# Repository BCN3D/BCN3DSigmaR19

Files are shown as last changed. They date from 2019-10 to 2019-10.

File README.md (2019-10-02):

## What’s hold in this repository?
This repository will hold all the information about the Mechanics of the BCN3D Sigma R19.
As a declared Open Source organization, it's in our mission to release all the original design files to you to be able to learn, reuse and improve. Open Source not only means code, it also concerns hardware.

We’ve managed to design and manufacture the BCN3D Sigma R19 thanks to our previous experience in the 3D printing industry, the ideas coming from the community, our engineering background and a narrow collaboration with our suppliers. Our goal is justify the decisions we took and share the know-how we acquired so far.

We also provide the source files for those who want to check the core of the BCN3D Sigma R19. You can consult both the CAD files and the technical drawings.

## CONCEPT DESIGN
During the concept design stage we set a clear target which determined the whole design and decisions: The BCN3D Sigma R19 is a professional printer.

### Aesthetics
It has to look  like a professional equipment. Our previous printers were made with aluminium extruded profiles and plastic printed parts. That made sense for printers oriented to makers or schools, sold as a kit. But, in this case, aesthetic was a major player. For this reason, we adopted a welded aluminium frame, which allows the Sigma to be a unique and attractive 3D printer

### Multimaterial
As a professional printer, it has to print as many materials as possible. Not only for engineers, who require tough -or flexible-, functional polymers, but also for designers who need the aesthetic component. However, material is not the only limitation. Complex geometries, overhangs and 3D printing doesn’t get along. So we wanted the Sigma to be a real solution for those users who need to print with supports as a must. In conclusion, the Sigma is the first and only commercial 3D printer with an Independent Dual Extuder (IDEX) system, which avoid all the side problems dual extrusion may cause.

### High Quality
The 3D Printing industry is maturing. Users are more and more demanding and 3D printing must be a solution, not a headache. For this reason, the Sigma has to be a reliable piece of engineering, easy to assemble, maintain and capable to print seamlessly high quality objects, no matter how complex they are.

### High Capacity
Real-life and functional parts are not always small. A big printing volume is a great advantage for a professional 3D Printer although the Sigma intends to be a desktop-sized printer. Allocating all the items and devices inside the frame, while granting ease-to-use and optimizing the axes structure were a key goal.

## DETAIL DESIGN INSIGHTS

We faced dozens of challenges during the design process. Below we describe some of them:

### Frame
Probably the biggest challenge. First we thought in a chassis made of profiles and then cover it. But then realized the cost in materials for that solution would be high enough to look for alternatives that could contribute more in the aesthetic field, even that could be a bit more expensive. On the other side, we wanted the Sigma to be an accessible printer, wide and open in order to ease the handling and operation. So we decided to explore the option of designing a unibody frame where all the mechanical components were mounted on and with a wide frontal oberture.

First we had to decide between using aluminium or steel. Steel offers many advantages: It’s a very stiff metal, great to build structures and precise mechanical systems. In addition, it’s easy to work with and cheap. But it’s -really- heavy. We contemplated the option of using a thinner metal sheet of steel for the frame. After ordering a prototype, we dismissed the idea, though. Still it had a great mechanical behaviour and a relative low weight, the feeling of touching a thin metal sheet (1.5mm) was unpleasant because it felt like a cutting edge. And it didn’t look sturdy. So to achieve both a reliable look and a pleasant contact, we needed to go up to 3mm thickness. But then the shipping costs would be absurdly high and the handling, a constant hassle -both during the assembly process and for the final user.

Aluminium, on the other hand, provides lightness and a smooth and sturdy look. But it’s more expensive as a material and it’s harder to laser cut and weld. After balancing pros and cons, we bet on aluminium option -although we had a plan B.

The second big issue to manage was the manufacturing process. We contemplated two different ways to do it: either manufacture the frame by parts and screw them all together in the assembly line or weld the frame. Welding aluminium is hard and the welding process itself has some thermal and geometric implications that have to be considered. But it allows to reduce the assembling time dramatically while it outsources a key process.

As alternative, designing the frame as separate parts to screw together was considerably cheaper - as you save a handmade process such as welding and polishing. But the assembling of the frame and adjustment could be very delicate and incompatible with our production tag time. So the overall cost wouldn’t be that different in both options. The aesthetic component, though, would be very penalized with this alternative, because we would need to add dozens of screws on the frame.

For these reasons, we finally opted for a welded structure. We sat hours with our supplier discussing the best way to design every single part in order to grant a proper alignment between the faces that would hold the axes. Furthermore, we also studied the mechanical behaviour of the frame with some CAE studies, simulating stress and deformations during a standard usage.

### High quality components
A good frame is not enough to achieve amazing results. In such a precision equipment as the Sigma, all the mechanical components play a key role. Due to the product requirements in terms of size and use of the internal space of the printer we had, we opted for a axes structure with the toolheads moving in the XY plane and an up and down moving Z axis.

With the XY plane decided to mount high precision linear guides. Despite its cost slightly higher than a system based on rods and bearings, the linear rails offer a professional look, an easy assembling and a compact package.

Regarding the Z axis, we were aware of the importance to have a robust guide system in order to avoid classic artifacts in printed parts related with a bad Z performance, such as Z wobbling. We also had experience using couplings and to connect the actuator with the leadscrew and we knew that a bad assembling could cause poor quality results. With this background, we chose using Ø12mm guide rods and a stepper motor with an inserted leadscrew. The whole system provides a high repeatability and accuracy.

### Independent Dual Extrusion
A 3D printer with such an specific feature increases the design unknowns and multiplies the components. Not only the firmware and the electronics need to be highly customized, but also mechanically there are some decisions to take.

First of all, because of the multiple components to hold, the internal parts tend to be more complex than other printers. So we decided to use aluminium sheet bending technology to manufacture the inner parts. As the manufacturing tolerances are acceptable for the purposes we intend and the technology is cheap and easily scalable, we considered the technology optimum.  

Two independent Extruders means have an extra moving stepper for the second toolhead, and the extra toolhead itself. On the other hand, when printing with both extruders it’s important to have a bucket to purge the idle hotends before start printing the model again. All this parts add weight to a moving element, which is a problem to print fast because the high inertias may worsen the print quality. So we designed the X and Y Axis as light as possible, saving as many grams as possible with every single component. Not only weight is important when doubling the toolheads, but also space. So we decided to adopt a bowden-based feeding system and miniaturize all the items as much as possible.

### Big Printing Volume
The BCN3D Sigma R19 features 210x297x210mm printing volume. In order to provide such a big volume and a free space on both sides to park the idle toolhead, but still having a desktop-sized printer, we had to reorient the Z platform. The main issue to solve, though, was granting the stiffness of the structure with a big overhang of more than 300mm.

To prevent vibrations, we adopted high quality bearings with low clearance and we designed and  simulated a custom metal sheet structure, which allows to get a great quality prints with a smooth surface despite the big overhang.

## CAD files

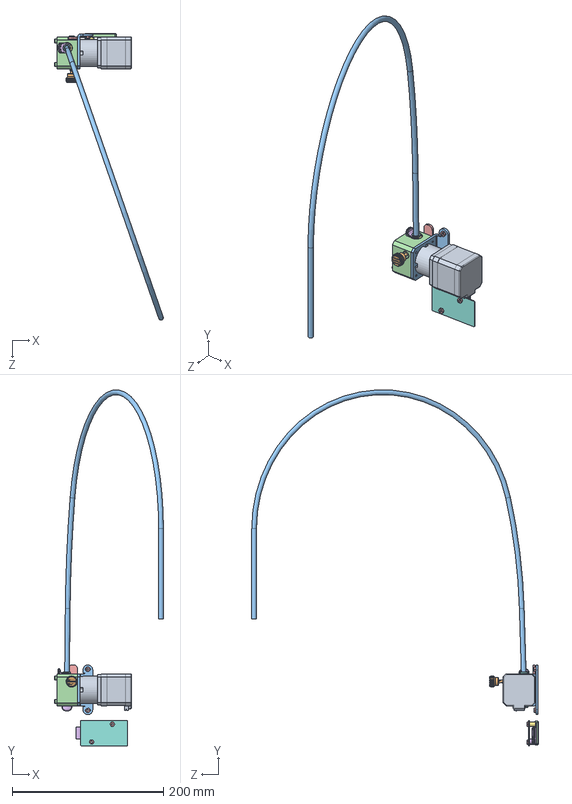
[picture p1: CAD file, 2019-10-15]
CAD/SW/040M07C01.0P000C Left extruder.SLDASM
143.8 x 470.4 x 378.6 mm
040M07C01.0P10A Nema 17 40mm
040M07C01.0P25Z Driving Gear
14080-a00_040M07C01.0P05E Extruder Stepper Holder
040M07C01.0P026E Extruder Body Left
040M07C01.0P027B Extruder Tensor Left
filament
10922-A00_Pneufit coupling x 2
10924-A00_Coupling collet x 2
Passador 4x24
BCN3DSigma-M05C01.0P08Z Purger Button
10982-A00_Bowden tube
A3DIN912 M3x30 x 3
A3DIN934 M3 x 4
040M04C00.0P03F Stepper Driver Board
Separador nylon negre 3.2x6x8 x 2
10918-A01_Extruder driver cover
A3DIN913 M3x3
DIN931 M4x50 (91280A154)
A3DIN912 M3x8 x 3
BCN3DSigma-M05C01.0P11F Driver spacer
BCN3DSigma-M04C00.0P09A Drivers Heatsink
BCN3DSigma-M07C01.0P14D Coupling Clip x 2

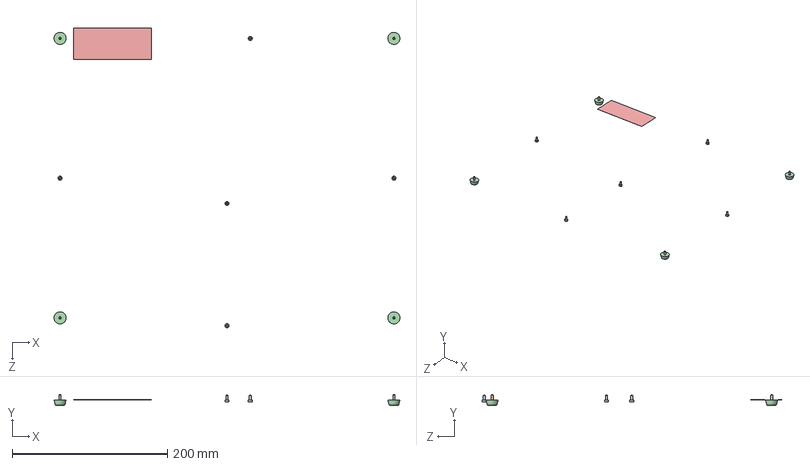
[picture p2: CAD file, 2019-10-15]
CAD/SW/BCN3DSigma-M01C03.0P000 Bottom cover.SLDASM
445.7 x 13.7 x 385.8 mm
DIN912 M3x6 x 5
DIN912 M3x10 x 4
DIN125 M3 x 4
BCN3DSigma-M01C03.0P02Z Leg x 4
BCN3DSigma-M01C01.0P25A Sigma CE Label

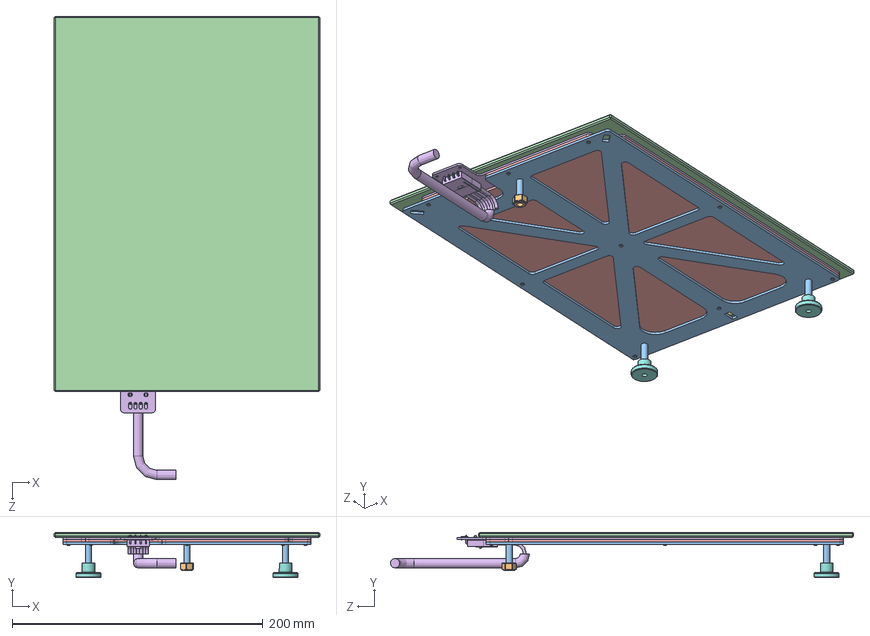
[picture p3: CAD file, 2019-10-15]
CAD/SW/BCN3DSigma-M03C02.0P000 Printing surface.SLDASM
212.0 x 36.1 x 369.2 mm
DIN7991 M3x6 x 9
DIN985 M5
10832-A00_Upper Platform
10906-A00_Cork
10908-A00_Heated bed
10888-A00 Bed Thumbscrew x 2
BCN3DSigma-M03C02.0P09A Thumbscrew Label x 2

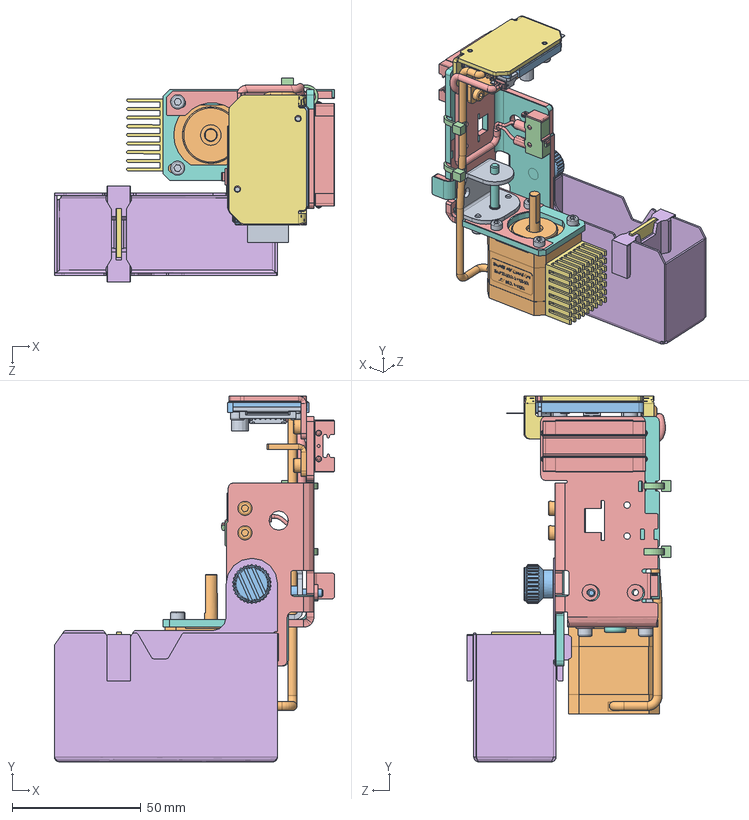
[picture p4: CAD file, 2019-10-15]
CAD/SW/BCN3DSigma-M05C02.0P000 X Axis Right.SLDASM
108.7 x 141.9 x 79.2 mm
DIN912 M3x6 x 8
DIN912 M3x8 x 6
DIN125 M3 poliamida x 2
DIN125 M3 x 2
10850-B00_Purger base right
040M05C02.0P04B X Stepper Driver Holder Right
BCN3DSigma-M02C01.0P10A Idler pulley shaft
BCN3DSigma-M04C00.0P03F Stepper Driver Board
10901-A00_Nema 14
BCN3DSigma-M05C01.0P08Z Purger Button
BCN3DSigma-M09C00.0P20A Zip tie x 2
Linear guide slide
Sigma_R17-M05C01.0P14D Cloth Support
BCN3DSigma-M05C01.0P07C Silicone Cloth
10828-A00_Stepper Holder Right
10830-B01_X Axis Idler
BCN3DSigma-M05C01.0P01D Belt Clamp
BCN3DSigma-M05C01.0P11F Driver spacer
BCN3DSigma-M02C01.0P08Z Endstop
BCN3DSigma-M09C00.0P15A Endstop X Right
BCN3DSigma-M04C00.0P09A Drivers Heatsink
040M05C01.0P017Z Heatsink 28x28x15

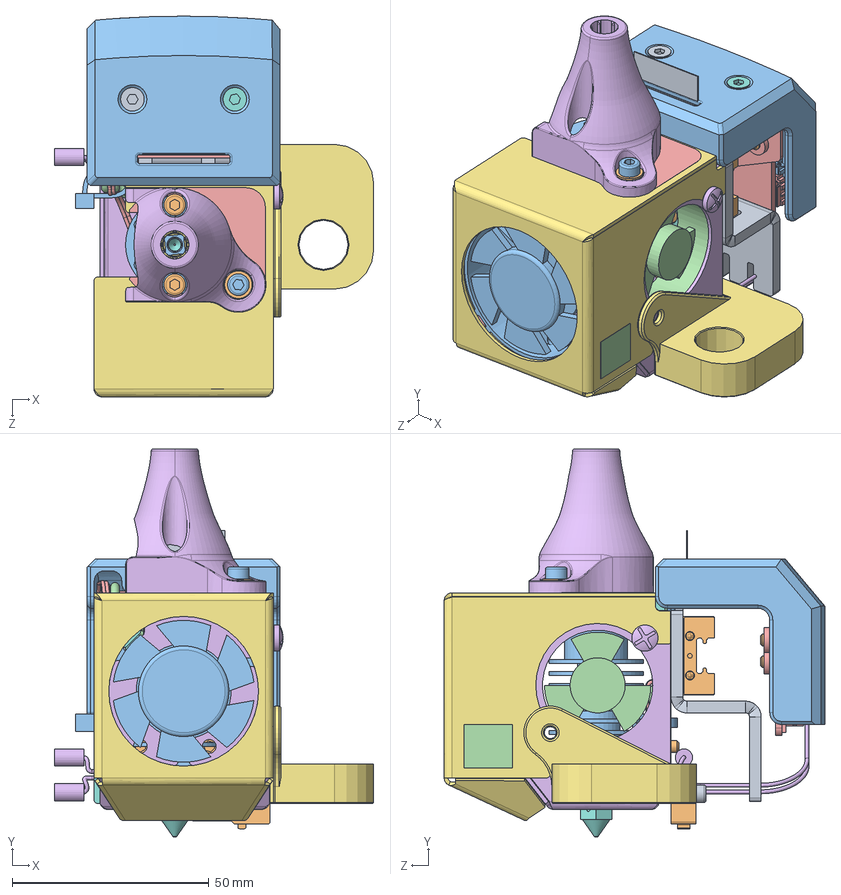
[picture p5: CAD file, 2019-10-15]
CAD/SW/040M06C01.0P000 Left Hotend.SLDASM
81.1 x 98.5 x 96.7 mm
A3DIN912 M2,5x10 x 2
A3DIN912 M3x6 x 8
A3DIN912 M3x10
A3DIN912 M3x8 x 2
A3DIN912 M3x18 x 3
A3DIN7981 9.5x3.2_RationalStock
A3DIN125 M3 poliamida x 4
A3DIN7991 M3x12
DIN7991 M3x12
A3DIN125 M3
BCN3DSigma-M06C01.0P01I Conexion Cover
040M06C01.0P03Z Heat sink fan
040M06C01.0P04C Connection board support
040M06C01.0P05E Lower cover
040M06C01.0P06D Upper cover
040M06C01.0P07D Hotend Plate
BCN3DSigma-M06C01.0P08F X Plate Left
040M06C01.0P09Z Layer fan
BCN3DSigma-M06C01.0P12B Layer fan spacer
040M04C00.0P04B Hotend Board
040M09C00.0P16B Endstop Z Left
A3DIN913 M3x3 x 2
040M06C03.0P01C Nozzle 0.4
040M06C03.0P02C Heatbreak
040M06C03.0P03A Hot block
040M06C03.0P04G Heatsink bowden
040M06C03.1P01B Resistance 24V
040M06C03.1P02B Thermistor
040M07C01.0P19Z Coupling collet
BCN3DSigma-M07C01.0P14D Coupling Clip
A3Connexio cable pla hotend
040M05C00.0P02ALinear guide slide
040M09C00.0P20A Zip tie
040M06C01.0P14A Hot surface Label
Nozzel Offset Shim 0.05mm A.5
040M06C01.0P15C Vertical bowden
Inductive Sensor Mount A1

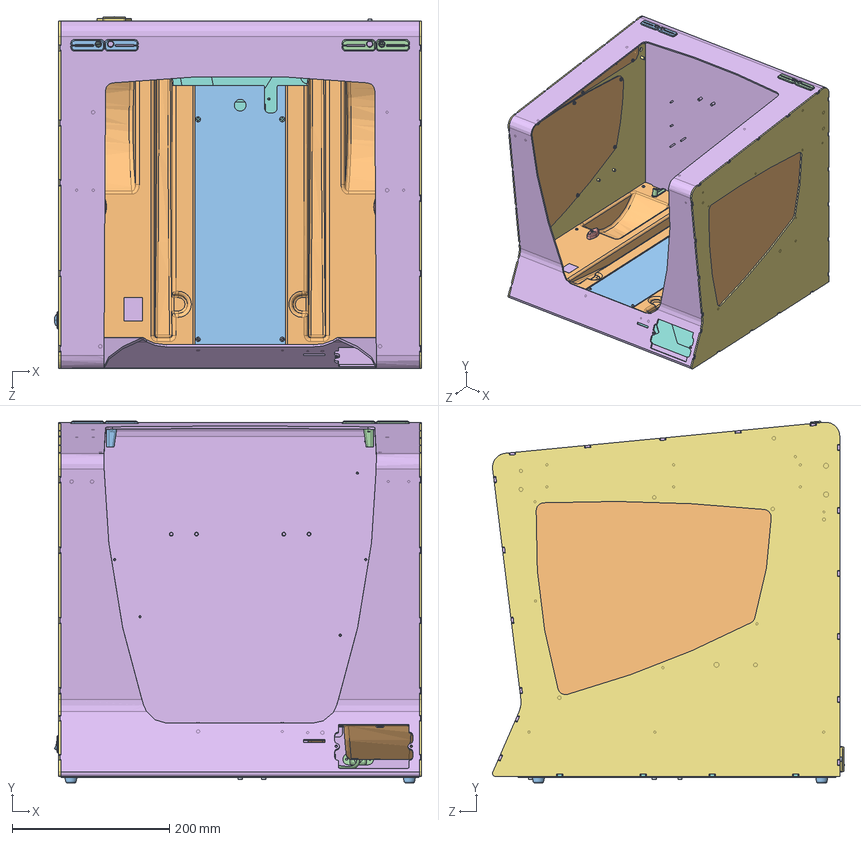
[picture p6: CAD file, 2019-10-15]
CAD/SW/BCN3DSigma-M01C00.0P000 Structure.SLDASM
466.9 x 459.6 x 447.2 mm
DIN125 M3 poliamida x 14
DIN934 M3 x 44
BCN3DSigma-M01C01.0P01J (RiT - Reverse Engineered) Top frame
BCN3DSigma-M01C01.0P03D (Test) Left_Right side x 2
BCN3DSigma-M01C01.0P02D (Test) Bottom frame
BCN3DSigma-M01C01.0P05D Y Idler Tensioner x 2
10894-A00_Window x 2
BCN3DSigma-M01C01.0P11Z Power button
BCN3DSigma-M01C01.0P12Z USB Extension Cable
BCN3DSigma-M01C01.0P20C Front LED connector clamp x 2
BCN3DSigma-M01C01.0P26C Hot bed cable double clip
BCN3DSigma-M04C00.0P07Z Power Entry Filter
BCN3DSigma-M01C01.0P17Z Fusible
BCN3DSigma-M01C01.0P30C Curve flat cable holder x 2
BCN3DSigma-M01C01.0P07G (Test) Guide spacer x 2
BCN3DSigma-M01C01.0P29H Bowden exit Left
BCN3DSigma-M01C01.0P29H Bowden exit Right
BCN3DSigma-M01C01.0P22D Plain flat cable holder x 4
BCN3DSigma-M01C01.0P15A Square 90 x 8
BCN3DSigma-M01C01.0P16A Square 60 x 2
DIN7981 3.2x9.5 x 6
ISO7380 M3x10 x 10
10890-A00_Inner cover 1.5mm
10891-A00_Electronics cover
BCN3DSigma-M01C02.0P06D Bowden entry guide x 2
BCN3DSigma-M01C02.P07F Bowden entry x 2
BCN3DSigma-M01C02.0P09A Crush Label
040M07C01.0P19Z Coupling collet x 2
10893-A00_Bottom cover
DIN912 M3x6 x 5
DIN912 M3x10 x 4
DIN125 M3 x 4
BCN3DSigma-M01C03.0P02Z Leg x 4
BCN3DSigma-M01C01.0P25A Sigma CE Label

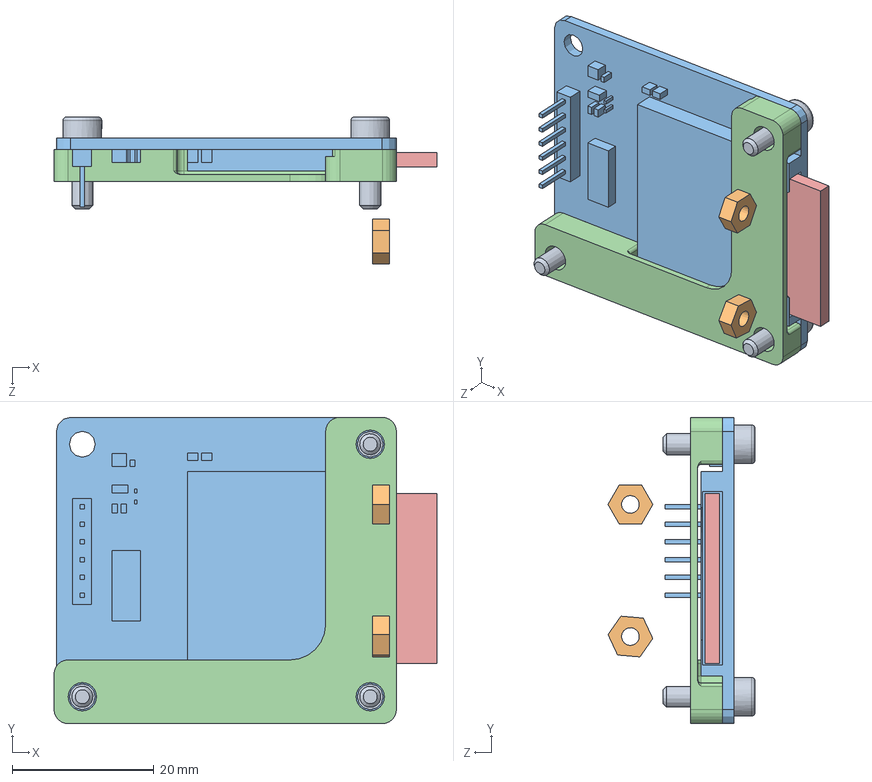
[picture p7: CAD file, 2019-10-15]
CAD/SW/BCN3DSigma-M04C02.0P000 SD Unit.SLDASM
54.1 x 43.2 x 20.8 mm
DIN912 M3x10 x 3
DIN934 M3 x 2
BCN3DSigma-M04C02.0P02AA SD module
BCN3DSigma-M04C02.0P03A SD spacer
BCN3DSigma-M04C02.0P04Z SD Card 8GB

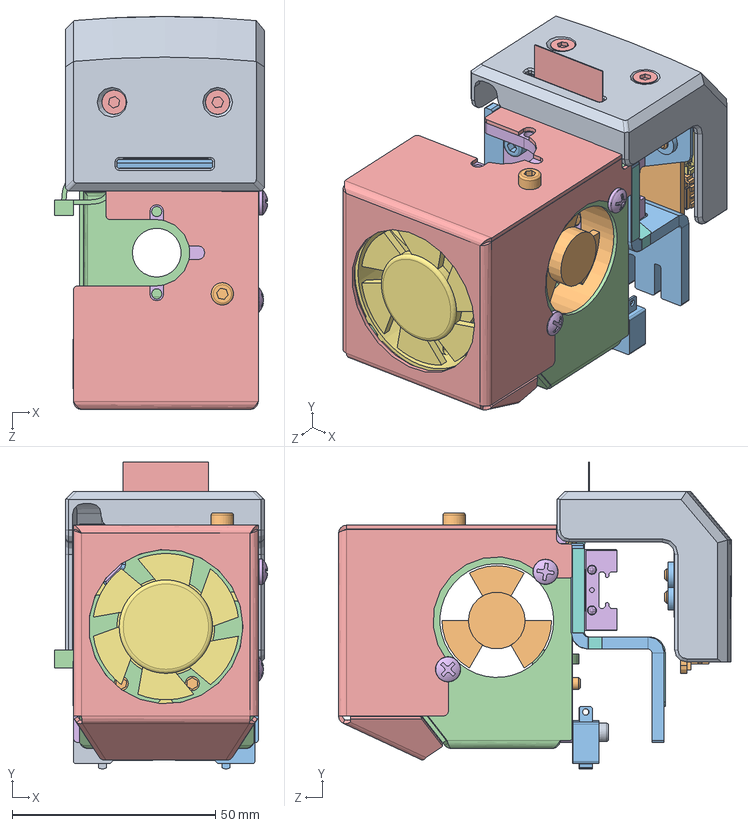
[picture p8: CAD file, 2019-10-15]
CAD/SW/BCN3DSigma-M06C02.0P000 Right Hotend.SLDASM
52.5 x 75.5 x 96.8 mm
DIN912 M2,5x10 x 2
DIN912 M3x6 x 7
DIN912 M3x8 x 2
DIN912 M3x18 x 3
DIN7991 M3x12 x 2
DIN7981 9.5x3.2 x 2
DIN125 M3 poliamida x 4
10852-A01_X Plate Right
BCN3DSigma-M06C01.0P01I Conexion Cover
11034-A00_Heat sink fan
10853-A01_Connection board support
10835-A01_Lower cover
BCN3DSigma-M06C01.0P06D Upper cover
BCN3DSigma-M06C01.0P07D Hotend Plate
10916-A00_Layer fan
BCN3DSigma-M06C01.0P12B Layer fan spacer
BCN3DSigma-M02C01.0P08Z Endstop
BCN3DSigma-M04C00.0P04B Hotend Board
BCN3DSigma-M09C00.0P16B Endstop Z Right
BCN3DSigma-M09C00.0P20A Zip tie
Connexio cable pla hotend
Linear guide slide
11004-A00_Hot surface Label

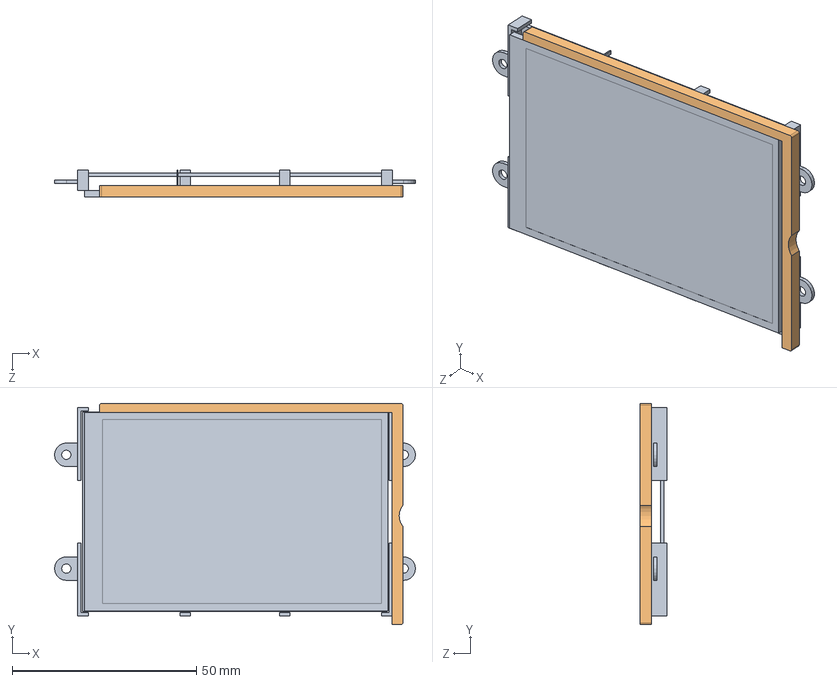
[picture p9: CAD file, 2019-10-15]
CAD/SW/BCN3DSigma-M04C01.0P000 Screen.SLDASM
97.8 x 60.0 x 7.20 mm
BCN3DSigma-M04C01.0P05Z LCD Touchscreen
BCN3DSigma-M04C01.0P07B Screen Positioner

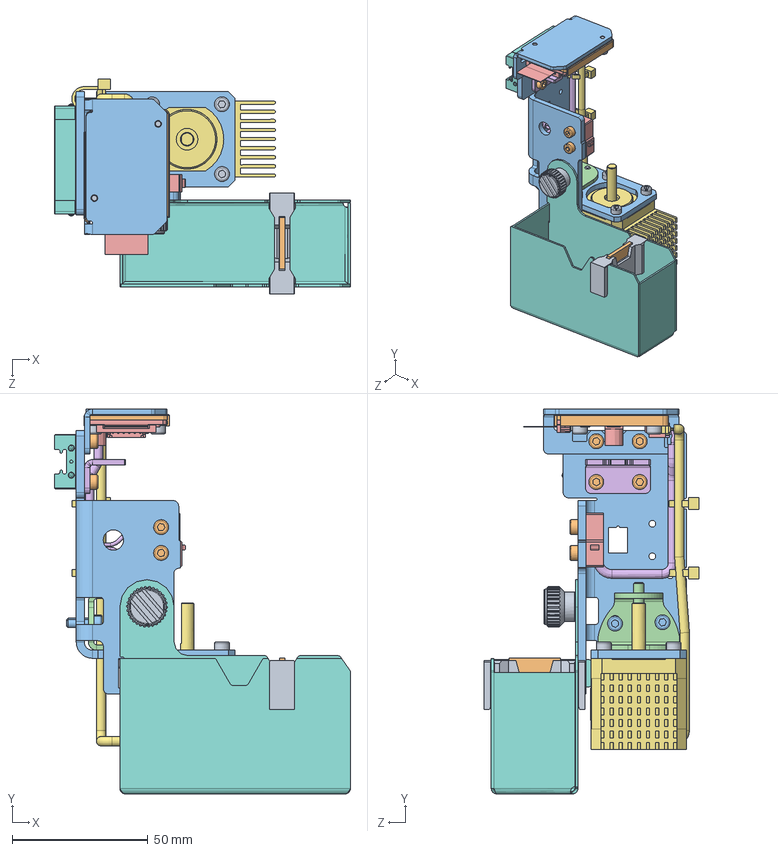
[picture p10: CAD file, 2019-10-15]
CAD/SW/BCN3DSigma-M05C01.0P000 X Axis Left.SLDASM
109.1 x 141.9 x 79.2 mm
DIN912 M3x6 x 8
DIN912 M3x8 x 6
DIN912 M3x10 x 2
DIN125 M3 poliamida x 2
DIN125 M3 x 2
10831-A00_Belt Clamp
10901-A00_Nema 14
10849-B00_Purger base left
BCN3DSigma-M05C01.0P08Z Purger Button
BCN3DSigma-M05C01.0P11F Driver spacer
BCN3DSigma-M05C01.0P12B X Stepper Driver Holder Left
BCN3DSigma-M02C01.0P10A Idler pulley shaft
BCN3DSigma-M04C00.0P03F Stepper Driver Board
BCN3DSigma-M09C00.0P15A Endstop X Left
BCN3DSigma-M09C00.0P20A Zip tie x 2
Linear guide slide
Sigma_R17-M05C01.0P14D Cloth Support
BCN3DSigma-M05C01.0P07C Silicone Cloth
10028-A00_Stepper Holder Left
10830-B01_X Axis Idler
BCN3DSigma-M02C01.0P08Z Endstop
BCN3DSigma-M04C00.0P09A Drivers Heatsink
040M05C01.0P017Z Heatsink 28x28x15

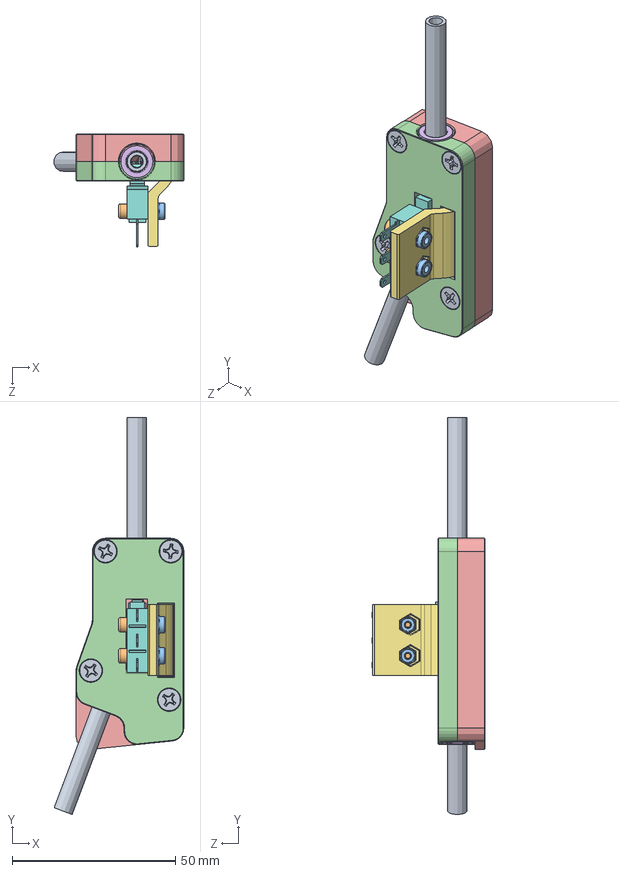
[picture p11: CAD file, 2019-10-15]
CAD/SW/040M07C04.0P000 Filament Runout Sensor Sigma.SLDASM
39.7 x 121.5 x 34.6 mm
DIN7982 M3.5x13 x 4
A3DIN912 M2,5x10 x 2
A3DIN985 M2.5 x 2
040M07C04.0P001F Body Mount
040M07C04.0P003D Body Cap Sigma
040M07C01.0P19Z Coupling collet x 2
040M07C04.0P005E Endstop Support
BCN3DSigma-M07C03.0P002Z Endstop
040M07C03.0P02C Extruder bowden x 2

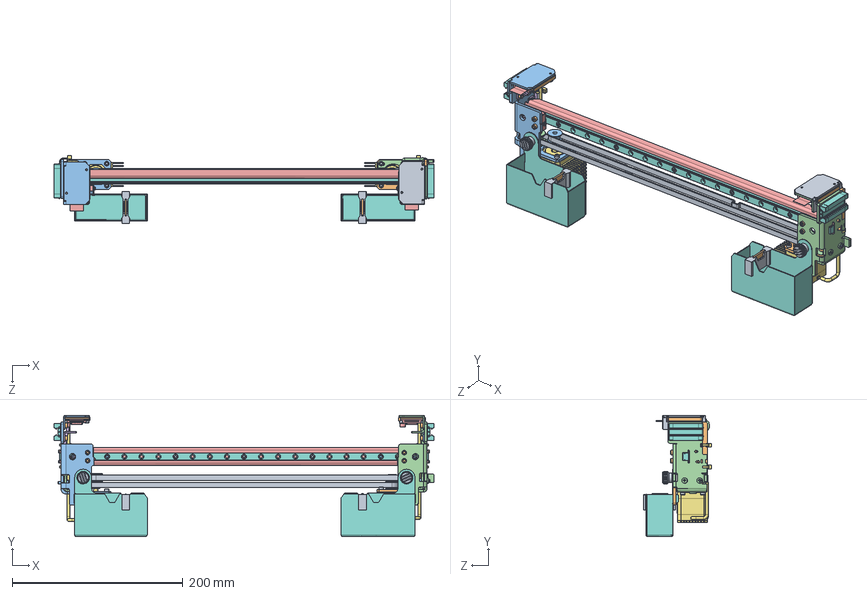
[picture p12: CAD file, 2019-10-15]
CAD/SW/BCN3DSigma-M05C00.0P000 X Axis.SLDASM
444.5 x 141.9 x 79.2 mm
DIN912 M3x6 x 19
DIN912 M3x8 x 16
DIN912 M3x10 x 7
DIN125 M3 poliamida x 4
DIN125 M3 x 4
10831-A00_Belt Clamp
10901-A00_Nema 14 x 2
10849-B00_Purger base left
BCN3DSigma-M05C01.0P08Z Purger Button x 2
BCN3DSigma-M05C01.0P11F Driver spacer x 2
BCN3DSigma-M05C01.0P12B X Stepper Driver Holder Left
BCN3DSigma-M02C01.0P10A Idler pulley shaft x 2
BCN3DSigma-M04C00.0P03F Stepper Driver Board x 2
BCN3DSigma-M09C00.0P15A Endstop X Left
BCN3DSigma-M09C00.0P20A Zip tie x 4
Linear guide slide x 2
Sigma_R17-M05C01.0P14D Cloth Support x 2
BCN3DSigma-M05C01.0P07C Silicone Cloth x 2
10028-A00_Stepper Holder Left
10830-B01_X Axis Idler x 2
BCN3DSigma-M02C01.0P08Z Endstop x 2
BCN3DSigma-M04C00.0P09A Drivers Heatsink x 2
040M05C01.0P017Z Heatsink 28x28x15 x 2
10850-B00_Purger base right
040M05C02.0P04B X Stepper Driver Holder Right
10828-A00_Stepper Holder Right
BCN3DSigma-M05C01.0P01D Belt Clamp
BCN3DSigma-M09C00.0P15A Endstop X Right
10848-A01_X reinforcement
10846-A01_Xsupport x 2
10847-A01_connection plate x 2
BCN3DSigma-M05C03.0P04Z X Guide
BCN3DSigma-M05C00.0P01Z X Belt x 2
BCN3DSigma-M02C01.0P016Z Spacer 4x8x6 Essentra x 2
BCN3DSigma-M05C01.0P15Z GT2 Pulley Ø5 Bore 6 Runice x 2
BCN3DSigma-M02C01.0P15Z GT2 Pulley Ø4 Bearing Bore 6 Runice x 2

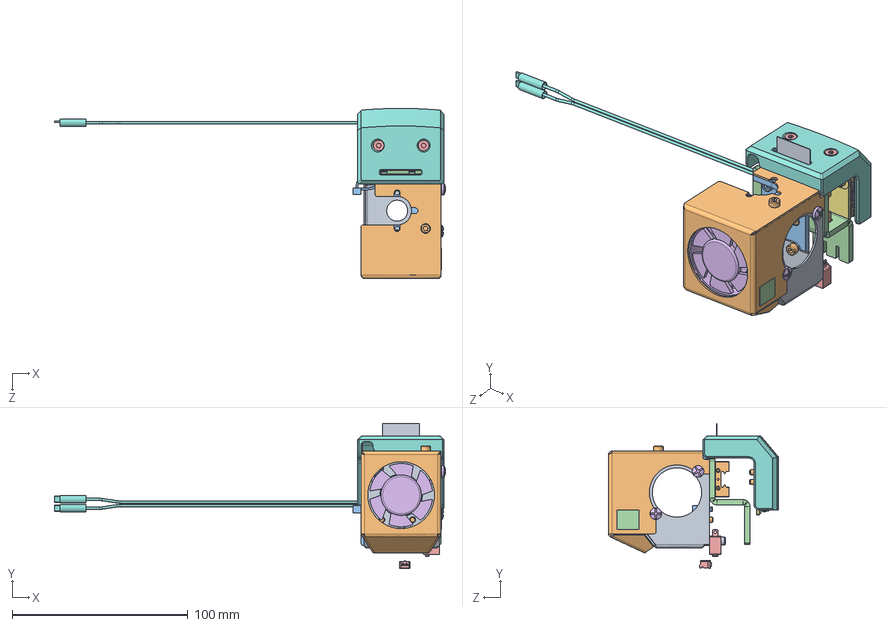
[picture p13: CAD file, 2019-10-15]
CAD/SW/BCN3DSigma-M06C01.0P000 Left Hotend.SLDASM
222.2 x 82.5 x 96.8 mm
DIN912 M2,5x10 x 2
DIN912 M3x6 x 7
DIN912 M3x8 x 2
DIN912 M3x18 x 3
DIN7991 M3x12 x 2
DIN7981 9.5x3.2_RationalStock x 2
DIN125 M3 poliamida x 4
BCN3DSigma-M06C01.0P01I Conexion Cover
040M06C01.0P05E Lower cover
10836-A01_Upper cover
BCN3DSigma-M06C01.0P07D Hotend Plate
10851-A00_X Plate Left
BCN3DSigma-M02C01.0P08Z Endstop
040M06C01.0P09Z Layer fan
BCN3DSigma-M04C00.0P04B Hotend Board
BCN3DSigma-M09C00.0P16E Z endstop cable
Connexio cable pla hotend
Linear guide slide
BCN3DSigma-M09C00.0P20A Zip tie
040M06C01.0P14A Hot surface Label
PHR-2

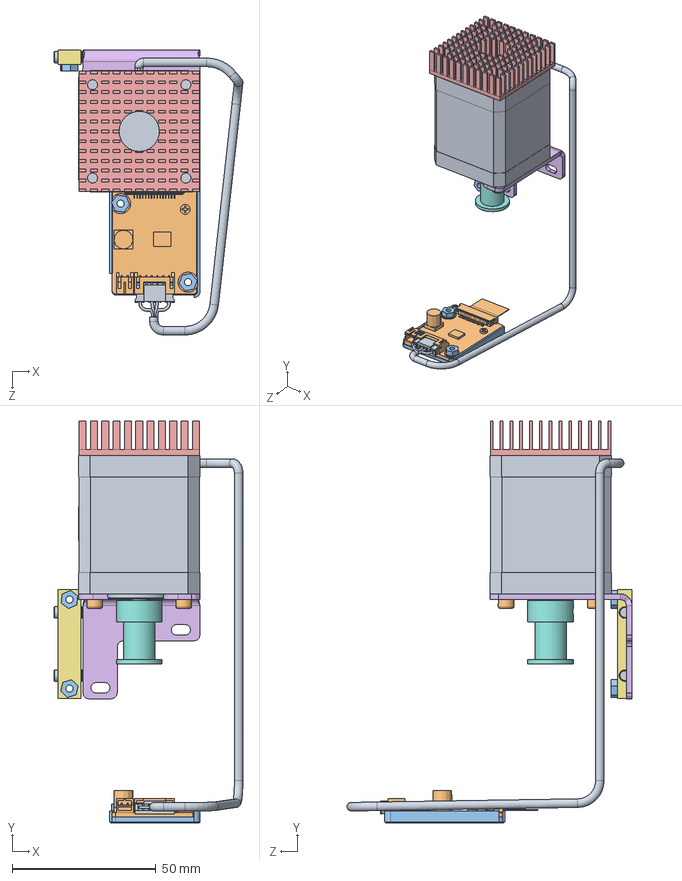
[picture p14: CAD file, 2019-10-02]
CAD/SW/BCN3DSigma-M02C02.0P000 Y Motor.SLDASM
65.8 x 139.9 x 99.3 mm
DIN913 M4x10 x 2
DIN912 M3x10 x 3
DIN934 M3 x 4
DIN913 M4x4 x 2
DIN125 M3 poliamida x 2
10854-A00_Y Stepper Holder
BCN3DSigma-M02C02.0P02C Y Belt tensor
BCN3DSigma-M02C02.0P07Z GT2 Pulley Ø5 Bore 12 Runice
BCN3DSigma-M02C02.0P06Z Nema17 47mm
BCN3DSigma-M04C00.0P03F Stepper Driver Board
BCN3DSigma-M05C01.0P11F Driver spacer
BCN3DSigma-M04C00.0P09A Drivers Heatsink
040M02C02.0P08Z 42x42x12

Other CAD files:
CAD/SW/040M07C04.0P000 Filament Runout Sensor.SLDASM
CAD/SW/Harness_1-BCN3DSigma-M06C01.0P000 Left Hotend.sldasm
CAD/SW/BCN3DSigma-M03C03.0P000 Z Motor.SLDASM
CAD/SW/040M05C01.0P000 X Axis Left.SLDASM
CAD/SW/022012065.SLDPRT
CAD/SW/022053061.SLDPRT
CAD/SW/039014040.SLDPRT
CAD/SW/040M01C02.0P000 Structure covers.SLDASM
CAD/SW/040M02C02.0P08Z 42x42x12.SLDPRT
CAD/SW/040M04C00.0P03F Stepper Driver Board.SLDPRT
CAD/SW/040M05C01.0P016D Jumbo Purge Bucket - Left.SLDPRT
CAD/SW/040M05C01.0P016D Jumbo Purge Bucket - Right.SLDPRT
CAD/SW/040M05C01.0P017Z Heatsink 28x28x15.SLDPRT
CAD/SW/040M05C01.0P08Z Purger Button.SLDPRT
CAD/SW/040M05C02.0P04B X Stepper Driver Holder Right.SLDPRT
CAD/SW/040M06C01.0P03Z Heat sink fan.SLDPRT
CAD/SW/040M06C01.0P04C Connection board support.SLDPRT
CAD/SW/040M06C01.0P05E Lower cover.SLDPRT
CAD/SW/040M06C01.0P09Z Layer fan.SLDPRT
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

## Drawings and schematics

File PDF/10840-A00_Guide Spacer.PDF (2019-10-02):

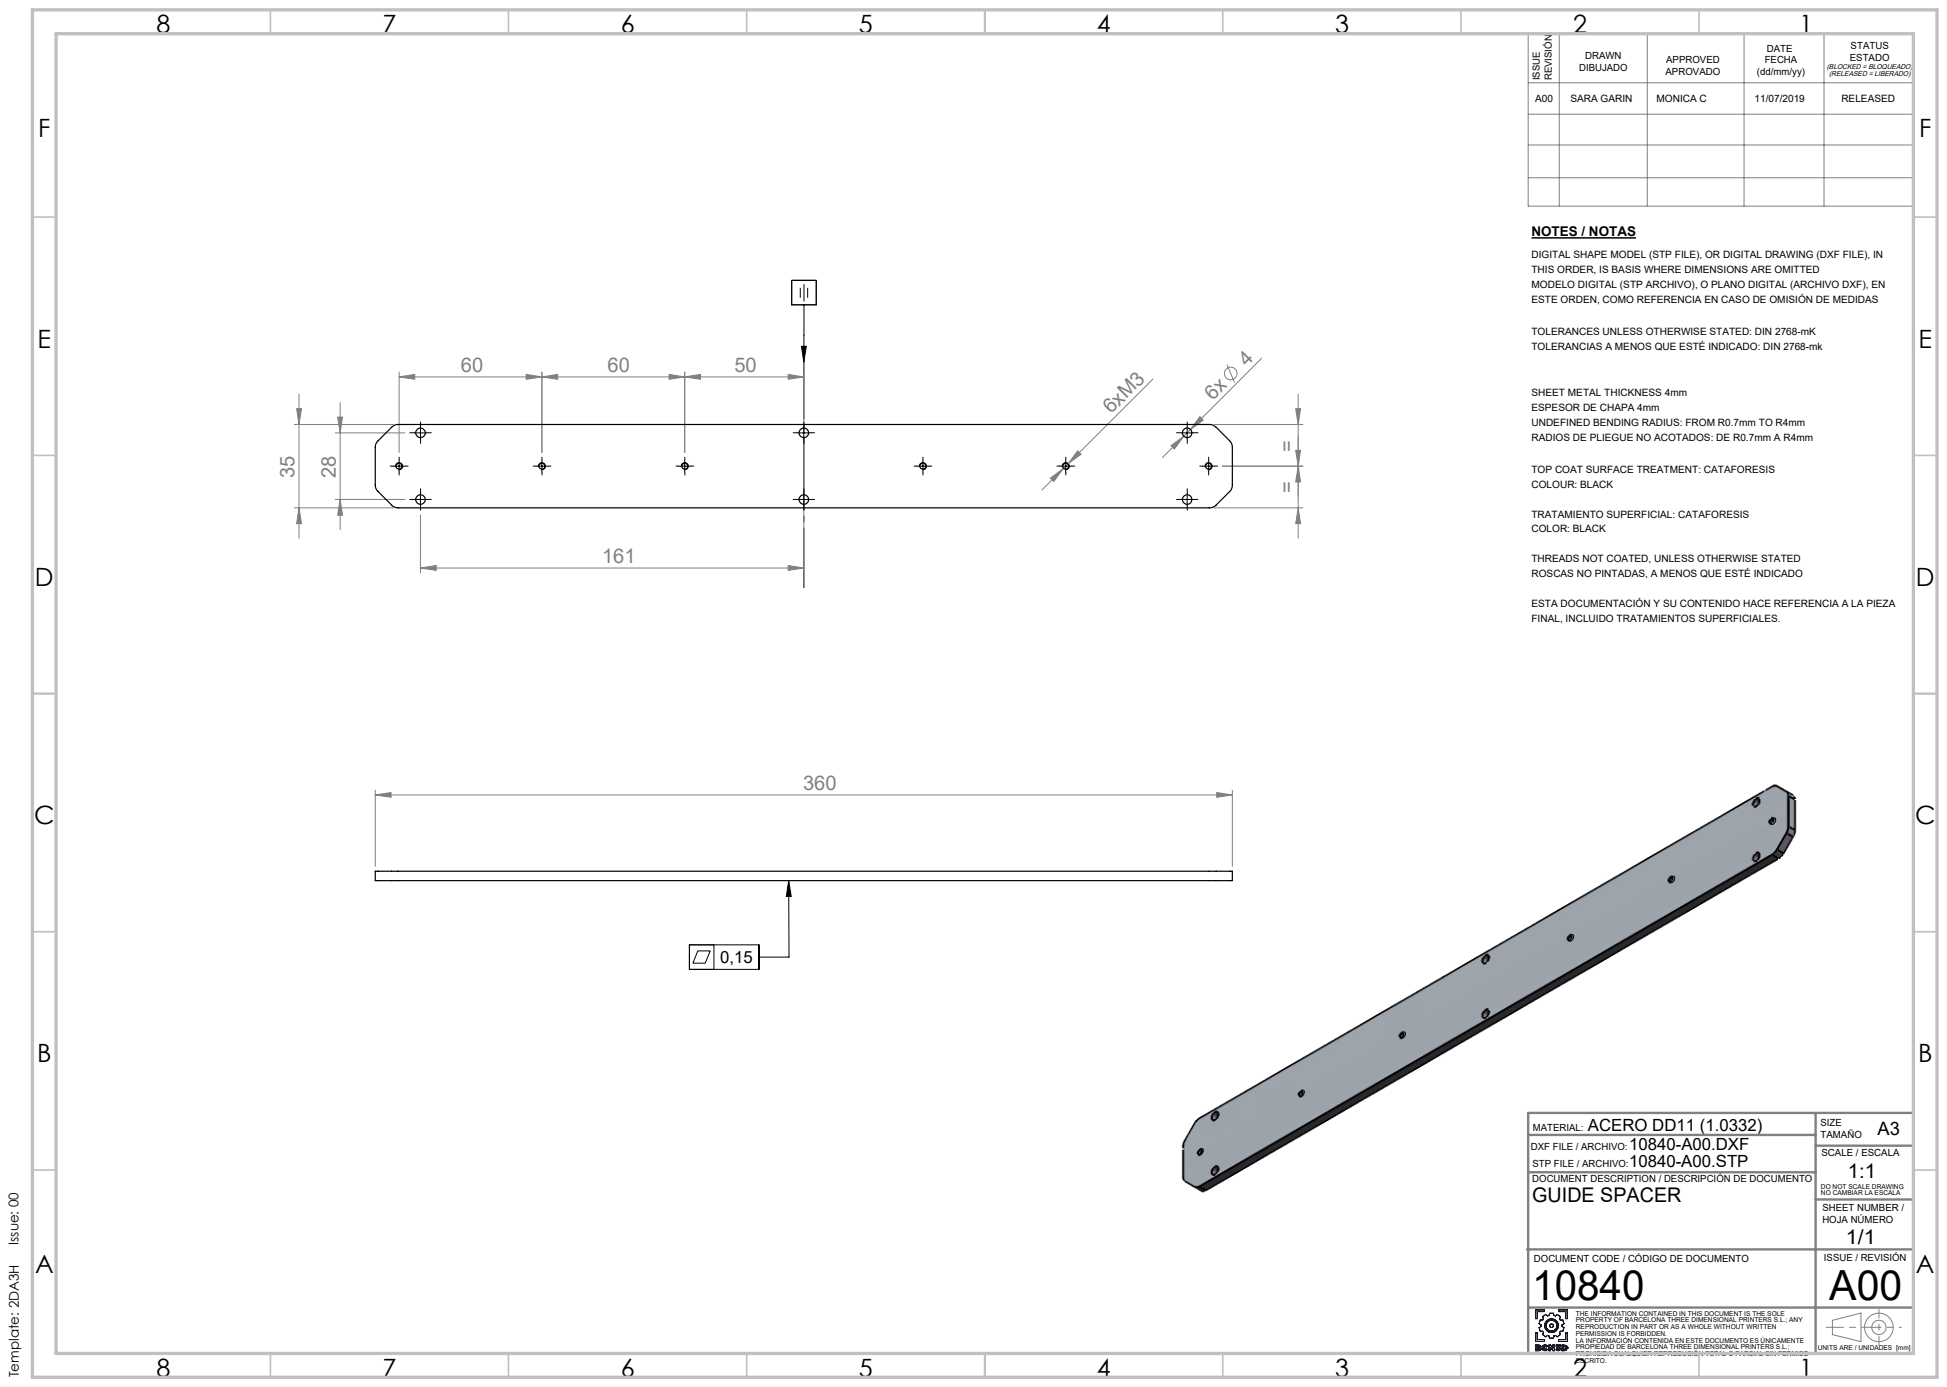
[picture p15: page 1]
SCALE / ESCALA; NOTES / NOTAS; Template: 2DA3H Issue: 00; ACERO DD11 (1.0332)

DRAWN DIBUJADO | APPROVED APROVADO | DATE FECHA (dd/mm/yy) | STATUS ESTADO (BLOCKED = BLOQUEADO) (RELEASED = LIBERADO)

A00 | SARA GARIN | MONICA C | 11/07/2019 | RELEASED

DIGITAL SHAPE MODEL (STP FILE), OR DIGITAL DRAWING (DXF FILE), IN
THIS ORDER, IS BASIS WHERE DIMENSIONS ARE OMITTED
MODELO DIGITAL (STP ARCHIVO), O PLANO DIGITAL (ARCHIVO DXF), EN
ESTE ORDEN, COMO REFERENCIA EN CASO DE OMISIÓN DE MEDIDAS

TOLERANCES UNLESS OTHERWISE STATED: DIN 2768-mK
TOLERANCIAS A MENOS QUE ESTÉ INDICADO: DIN 2768-mk

SHEET METAL THICKNESS 4mm
ESPESOR DE CHAPA 4mm
UNDEFINED BENDING RADIUS: FROM R0.7mm TO R4mm
RADIOS DE PLIEGUE NO ACOTADOS: DE R0.7mm A R4mm

TOP COAT SURFACE TREATMENT: CATAFORESIS
COLOUR: BLACK

TRATAMIENTO SUPERFICIAL: CATAFORESIS
COLOR: BLACK

THREADS NOT COATED, UNLESS OTHERWISE STATED
ROSCAS NO PINTADAS, A MENOS QUE ESTÉ INDICADO

ESTA DOCUMENTACIÓN Y SU CONTENIDO HACE REFERENCIA A LA PIEZA
FINAL, INCLUIDO TRATAMIENTOS SUPERFICIALES.

MATERIAL:
DXF FILE / ARCHIVO:
STP FILE / ARCHIVO:
DOCUMENT DESCRIPTION / DESCRIPCIÓN DE DOCUMENTO
GUIDE SPACER

DO NOT SCALE DRAWING
NO CAMBIAR LA ESCALA
SHEET NUMBER /
HOJA NÚMERO

DOCUMENT CODE / CÓDIGO DE DOCUMENTO 10840 | ISSUE / REVISIÓN A00

THE INFORMATION CONTAINED IN THIS DOCUMENT IS THE SOLE PROPERTY OF BARCELONA THREE DIMENSIONAL PRINTERS S.L.; ANY REPRODUCTION IN PART OR AS A WHOLE WITHOUT WRITTEN PERMISSION IS FORBIDDEN. LA INFORMACIÓN CONTENIDA EN ESTE DOCUMENTO ES ÚNICAMENTE PROPIEDAD DE BARCELONA THREE DIMENSIONAL PRINTERS S.L.; | UNITS ARE / UNIDADES [mm]

PROHIBIDA CUALQUIER REPRODUCIÓN TOTAL O PARCIAL SIN PERMISO

ESCRITO.

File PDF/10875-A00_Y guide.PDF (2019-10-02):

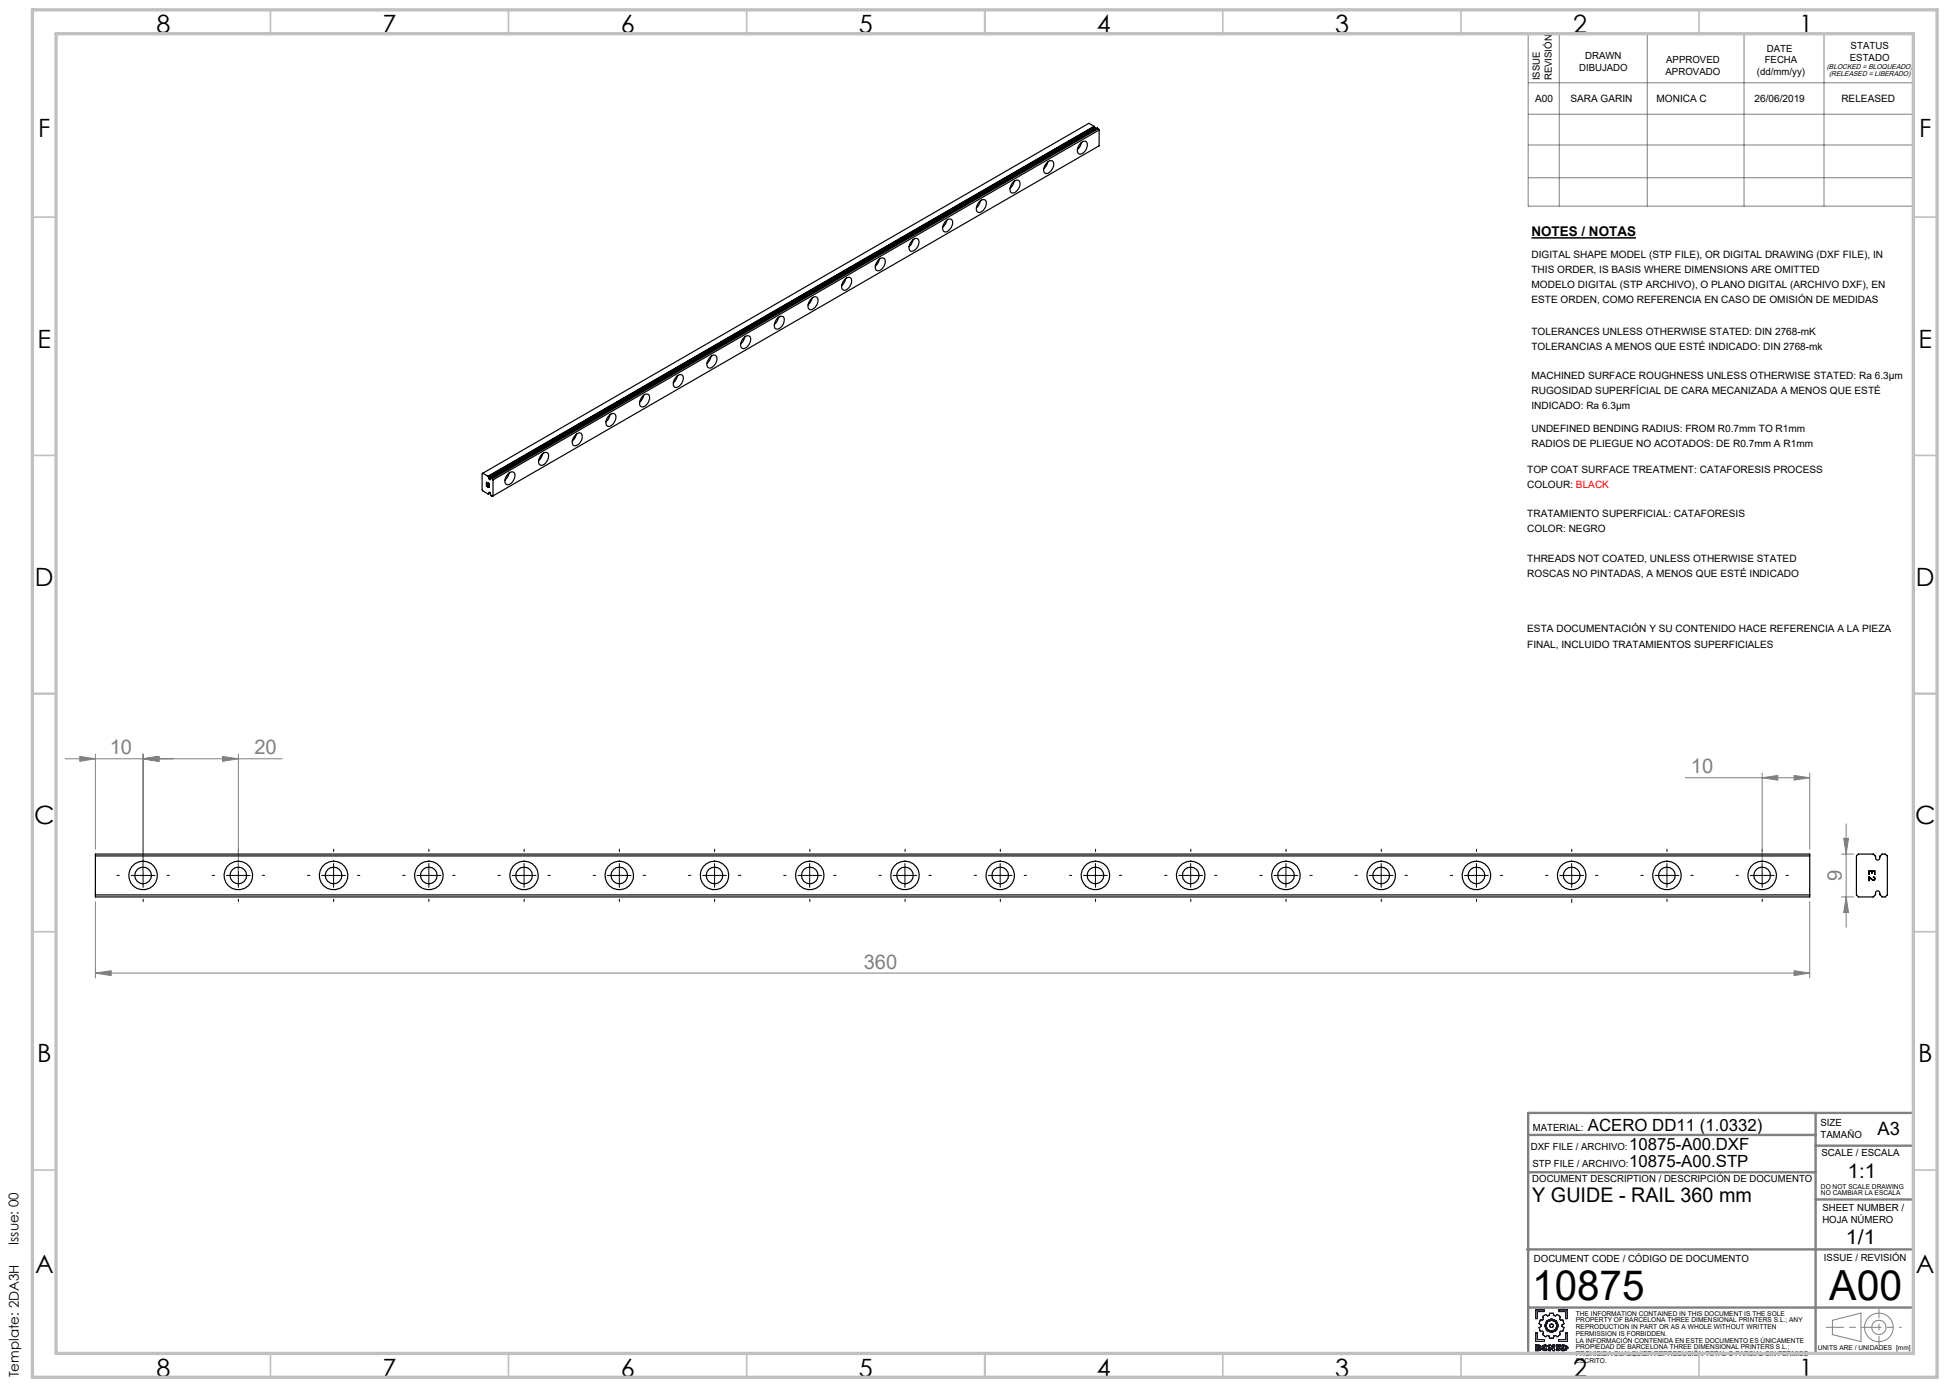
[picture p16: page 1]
SCALE / ESCALA; NOTES / NOTAS; Template: 2DA3H Issue: 00; ACERO DD11 (1.0332)

DRAWN DIBUJADO | APPROVED APROVADO | DATE FECHA (dd/mm/yy) | STATUS ESTADO (BLOCKED = BLOQUEADO) (RELEASED = LIBERADO)

A00 | SARA GARIN | MONICA C | 26/06/2019 | RELEASED

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

TOLERANCES UNLESS OTHERWISE STATED: DIN 2768-mK
TOLERANCIAS A MENOS QUE ESTÉ INDICADO: DIN 2768-mk

MACHINED SURFACE ROUGHNESS UNLESS OTHERWISE STATED: Ra 6.3µm
RUGOSIDAD SUPERFÍCIAL DE CARA MECANIZADA A MENOS QUE ESTÉ
INDICADO: Ra 6.3µm
UNDEFINED BENDING RADIUS: FROM R0.7mm TO R1mm
RADIOS DE PLIEGUE NO ACOTADOS: DE R0.7mm A R1mm

TOP COAT SURFACE TREATMENT: CATAFORESIS PROCESS
COLOUR: BLACK

TRATAMIENTO SUPERFICIAL: CATAFORESIS
COLOR: NEGRO

THREADS NOT COATED, UNLESS OTHERWISE STATED
ROSCAS NO PINTADAS, A MENOS QUE ESTÉ INDICADO

ESTA DOCUMENTACIÓN Y SU CONTENIDO HACE REFERENCIA A LA PIEZA
FINAL, INCLUIDO TRATAMIENTOS SUPERFICIALES

MATERIAL:
DXF FILE / ARCHIVO:
STP FILE / ARCHIVO:
DOCUMENT DESCRIPTION / DESCRIPCIÓN DE DOCUMENTO
Y GUIDE - RAIL 360 mm

DO NOT SCALE DRAWING
NO CAMBIAR LA ESCALA
SHEET NUMBER /
HOJA NÚMERO

DOCUMENT CODE / CÓDIGO DE DOCUMENTO 10875 | ISSUE / REVISIÓN A00

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

PROHIBIDA CUALQUIER REPRODUCIÓN TOTAL O PARCIAL SIN PERMISO

ESCRITO.

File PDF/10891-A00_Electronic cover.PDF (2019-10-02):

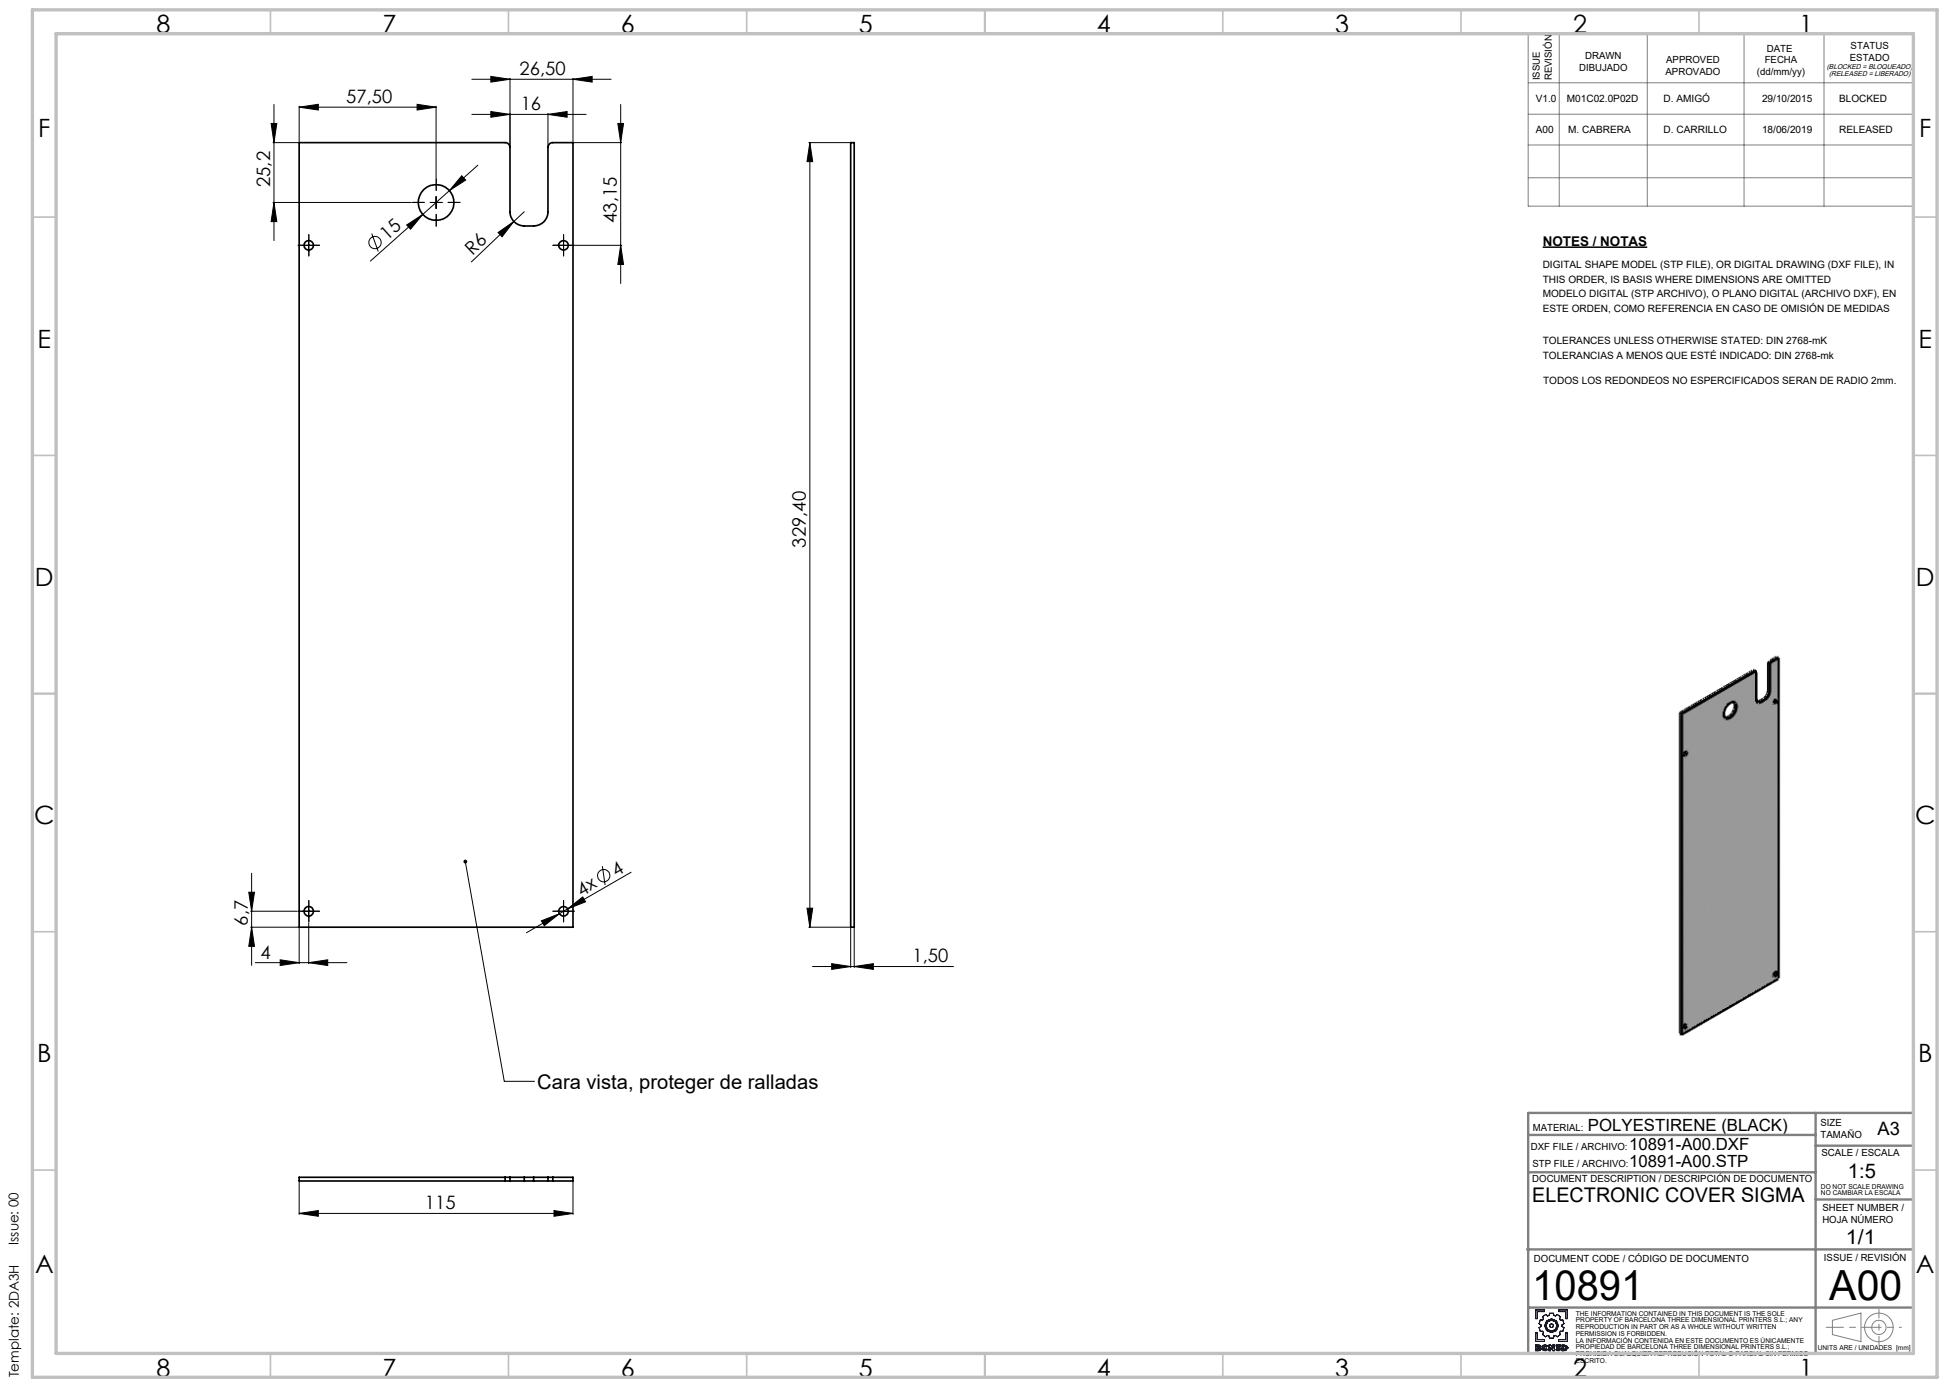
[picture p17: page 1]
SCALE / ESCALA; NOTES / NOTAS; Template: 2DA3H Issue: 00; POLYESTIRENE (BLACK)

DRAWN DIBUJADO | APPROVED APROVADO | DATE FECHA (dd/mm/yy) | STATUS ESTADO (BLOCKED = BLOQUEADO) (RELEASED = LIBERADO)

V1.0 | M01C02.0P02D | D. AMIGÓ | 29/10/2015 | BLOCKED

A00 | M. CABRERA | D. CARRILLO | 18/06/2019 | RELEASED

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

TOLERANCES UNLESS OTHERWISE STATED: DIN 2768-mK
TOLERANCIAS A MENOS QUE ESTÉ INDICADO: DIN 2768-mk
TODOS LOS REDONDEOS NO ESPERCIFICADOS SERAN DE RADIO 2mm.

Cara vista, proteger de ralladas

MATERIAL:
DXF FILE / ARCHIVO:
STP FILE / ARCHIVO:
DOCUMENT DESCRIPTION / DESCRIPCIÓN DE DOCUMENTO
ELECTRONIC COVER SIGMA

DO NOT SCALE DRAWING
NO CAMBIAR LA ESCALA
SHEET NUMBER /
HOJA NÚMERO

DOCUMENT CODE / CÓDIGO DE DOCUMENTO 10891 | ISSUE / REVISIÓN A00

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

PROHIBIDA CUALQUIER REPRODUCIÓN TOTAL O PARCIAL SIN PERMISO

ESCRITO.

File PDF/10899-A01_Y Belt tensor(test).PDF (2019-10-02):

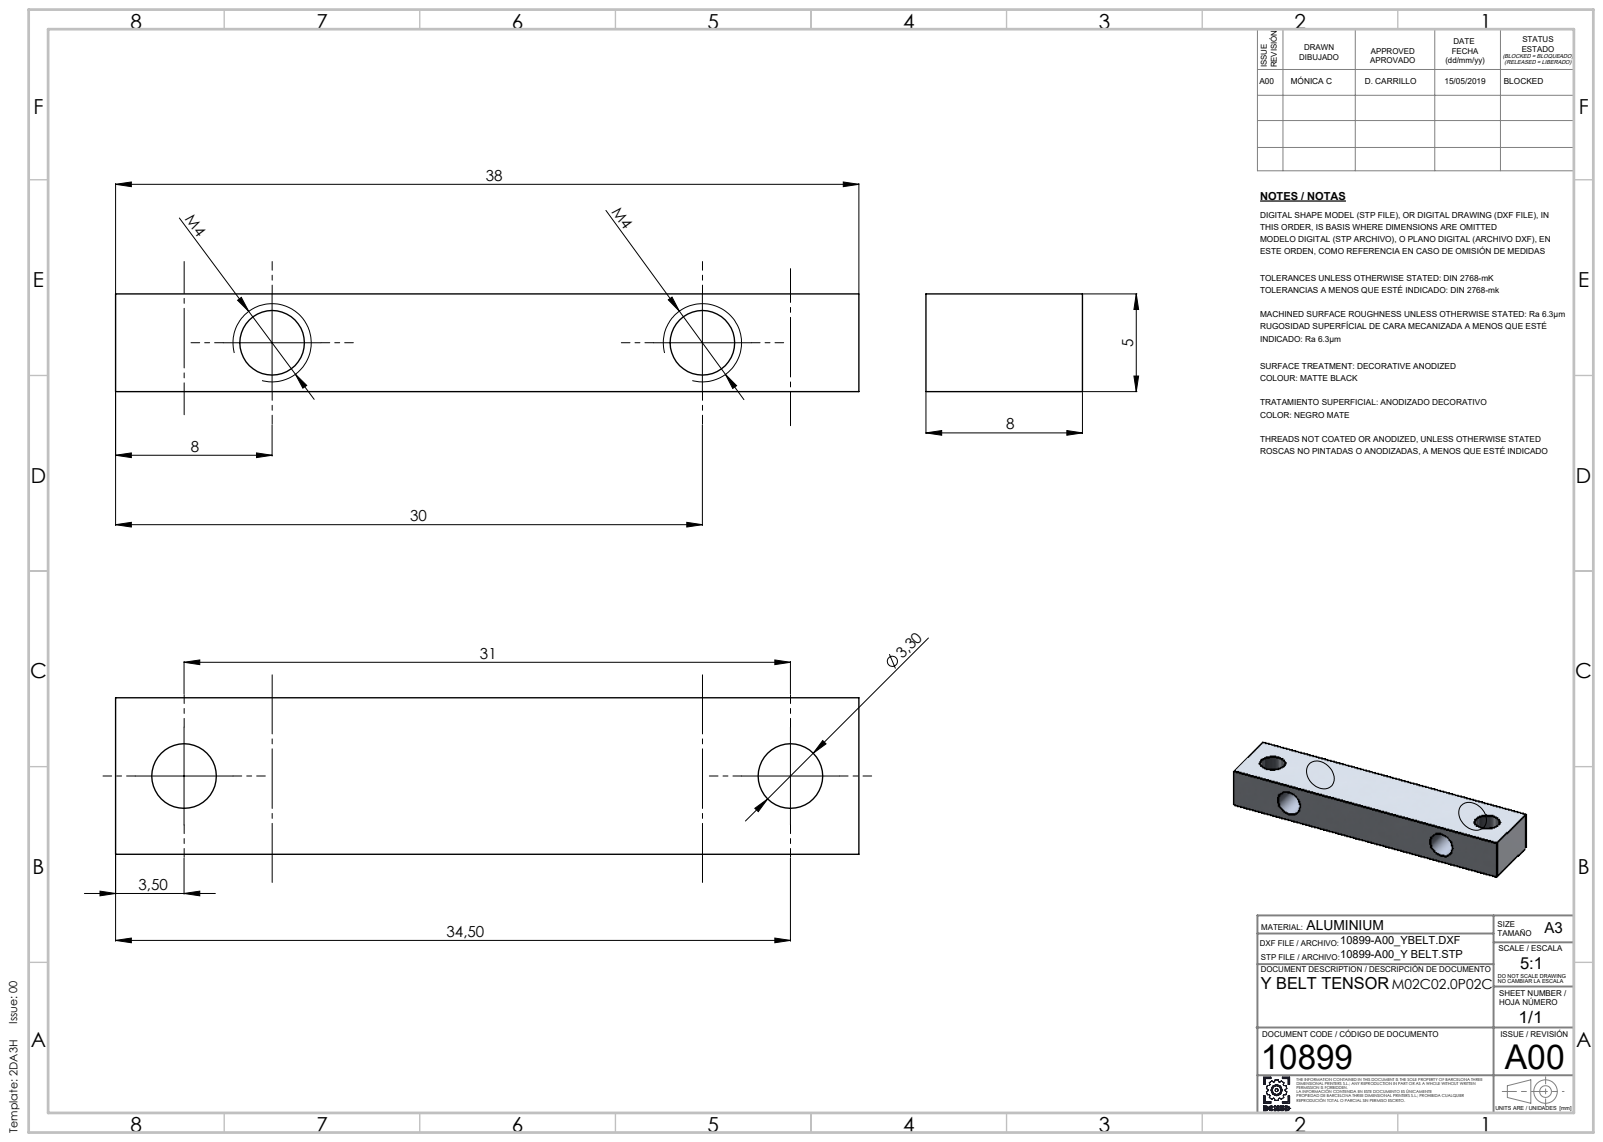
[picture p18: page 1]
SCALE / ESCALA; NOTES / NOTAS; Template: 2DA3H Issue: 00; 10899-A00_Y BELT.STP

38 | | DRAWN DIBUJADO | APPROVED APROVADO | DATE FECHA (dd/mm/yy) | STATUS ESTADO (BLOCKED = BLOQUEADO) (RELEASED = LIBERADO)

A00 | MÓNICA C | D. CARRILLO | 15/05/2019 | BLOCKED

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

TOLERANCES UNLESS OTHERWISE STATED: DIN 2768-mK
TOLERANCIAS A MENOS QUE ESTÉ INDICADO: DIN 2768-mk

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

SURFACE TREATMENT: DECORATIVE ANODIZED
COLOUR: MATTE BLACK

TRATAMIENTO SUPERFICIAL: ANODIZADO DECORATIVO
COLOR: NEGRO MATE

THREADS NOT COATED OR ANODIZED, UNLESS OTHERWISE STATED
ROSCAS NO PINTADAS O ANODIZADAS, A MENOS QUE ESTÉ INDICADO

MATERIAL:
DXF FILE / ARCHIVO:
STP FILE / ARCHIVO:
DOCUMENT DESCRIPTION / DESCRIPCIÓN DE DOCUMENTO
Y BELT TENSOR

DO NOT SCALE DRAWING
NO CAMBIAR LA ESCALA
SHEET NUMBER /
HOJA NÚMERO

DOCUMENT CODE / CÓDIGO DE DOCUMENTO 10899 | ISSUE / REVISIÓN A00

THE INFORMATION CONTAINED IN THIS DOCUMENT IS THE SOLE PROPERTY OF BARCELONA THREE DIMENSIONAL PRINTERS S.L.; ANY REPRODUCTION IN PART OR AS A WHOLE WITHOUT WRITTEN PERMISSION IS FORBIDDEN. LA INFORMACIÓN CONTENIDA EN ESTE DOCUMENTO ES ÚNICAMENTE PROPIEDAD DE BARCELONA THREE DIMENSIONAL PRINTERS S.L.; PROHIBIDA CUALQUIER REPRODUCIÓN TOTAL O PARCIAL SIN PERMISO ESCRITO. | UNITS ARE / UNIDADES [mm]

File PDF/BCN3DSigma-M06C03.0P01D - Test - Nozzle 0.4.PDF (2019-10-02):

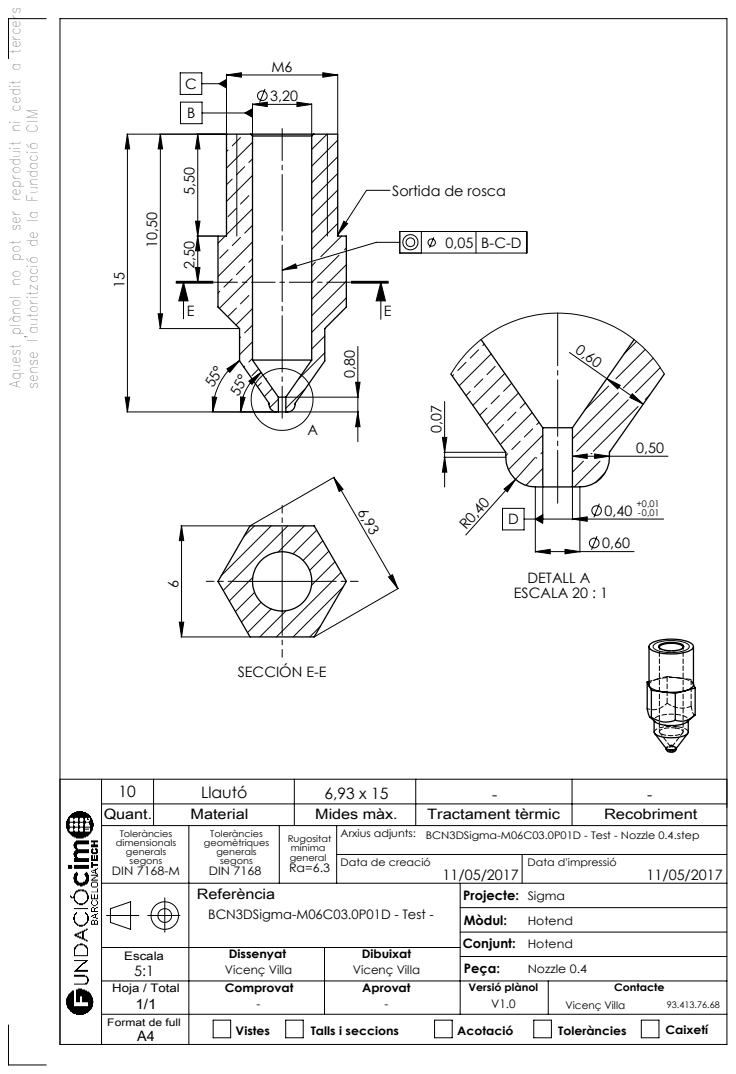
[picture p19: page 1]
Mides màx.; Tractament tèrmic; Recobriment; Data de creació; Data d'impressió; Vistes; Talls i seccions; Acotació; Toleràncies; Caixetí; Nozzle 0.4; DETALL A; ESCALA 20 : 1 D; SECCIÓN E-E

Aquest plànol no pot ser reproduit ni cedit a tercers

sense l'autorització de la Fundació CIM

Sortida de rosca

Toleràncies dimensionals generals segons DIN 7168-M | Toleràncies geomètriques generals segons DIN 7168 | Rugositat mínima general Ra=6.3 | Arxius adjunts: BCN3DSigma-M06C03.0P01D - Test - Nozzle 0.4.step

Referència BCN3DSigma-M06C03.0P01D - Test - | Projecte: Sigma Mòdul: Hotend Conjunt: Hotend

Escala 5:1 | Dissenyat Vicenç Villa | Dibuixat Vicenç Villa

Hoja / Total 1/1 | Comprovat - | Aprovat - | Versió plànol V1.0 | Contacte Vicenç Villa 93.413.76.68

Format de full A4

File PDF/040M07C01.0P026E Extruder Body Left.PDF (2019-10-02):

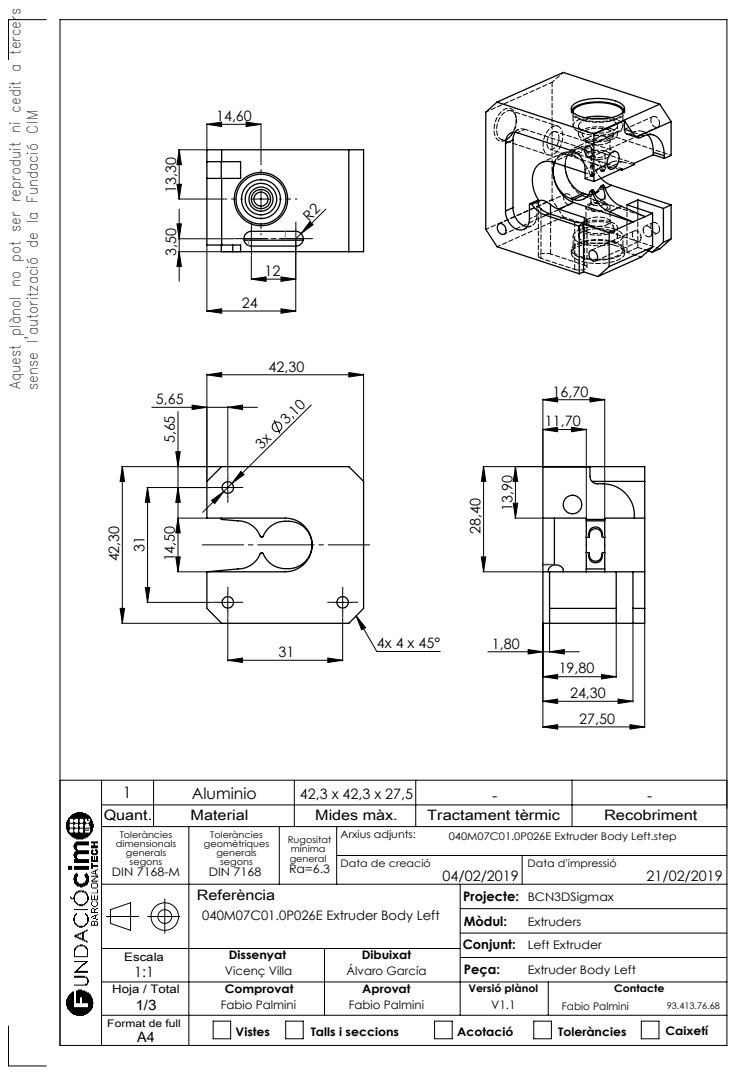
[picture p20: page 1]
Mides màx.; Tractament tèrmic; Recobriment; Data de creació; Data d'impressió; Vistes; Talls i seccions; Acotació; Toleràncies; Caixetí

Aquest plànol no pot ser reproduit ni cedit a tercers

sense l'autorització de la Fundació CIM

Toleràncies dimensionals generals segons DIN 7168-M | Toleràncies geomètriques generals segons DIN 7168 | Rugositat mínima general Ra=6.3 | Arxius adjunts: 040M07C01.0P026E Extruder Body Left.step

Referència 040M07C01.0P026E Extruder Body Left | Projecte: BCN3DSigmax Mòdul: Extruders Conjunt: Left Extruder

Escala 1:1 | Dissenyat Vicenç Villa | Dibuixat Álvaro García

Extruder Body Left

Hoja / Total | Comprovat Fabio Palmini | Aprovat Fabio Palmini | Versió plànol V1.1 | Contacte Fabio Palmini 93.413.76.68

Format de full A4

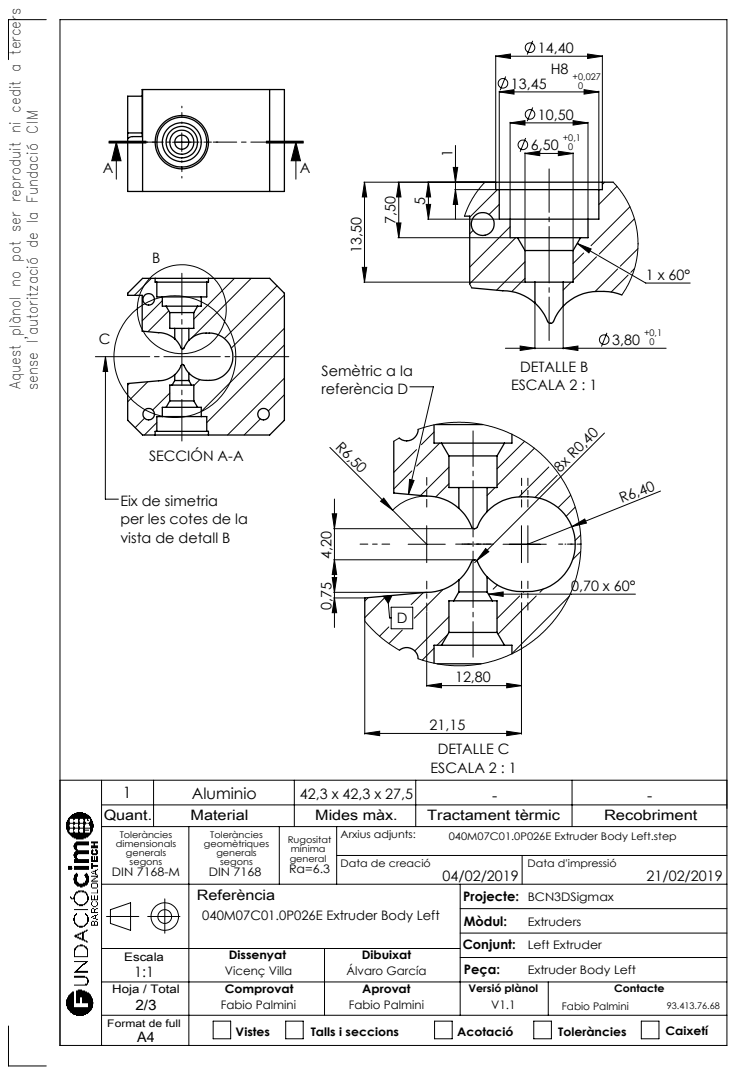
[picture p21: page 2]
Mides màx.; Tractament tèrmic; Recobriment; Data de creació; Data d'impressió; DETALLE B ESCALA 2 : 1; SECCIÓN A-A; DETALLE C ESCALA 2 : 1; Semètric a la referència DD

Aquest plànol no pot ser reproduit ni cedit a tercers

sense l'autorització de la Fundació CIM

Eix de simetria
per les cotes de la
vista de detall B

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

Referència 040M07C01.0P026E Extruder Body Left | Projecte: BCN3DSigmax Mòdul: Extruders Conjunt: Left Extruder

Escala 1:1 | Dissenyat Vicenç Villa | Dibuixat Álvaro García

Extruder Body Left

Hoja / Total | Comprovat | Aprovat | Versió plànol | Contacte

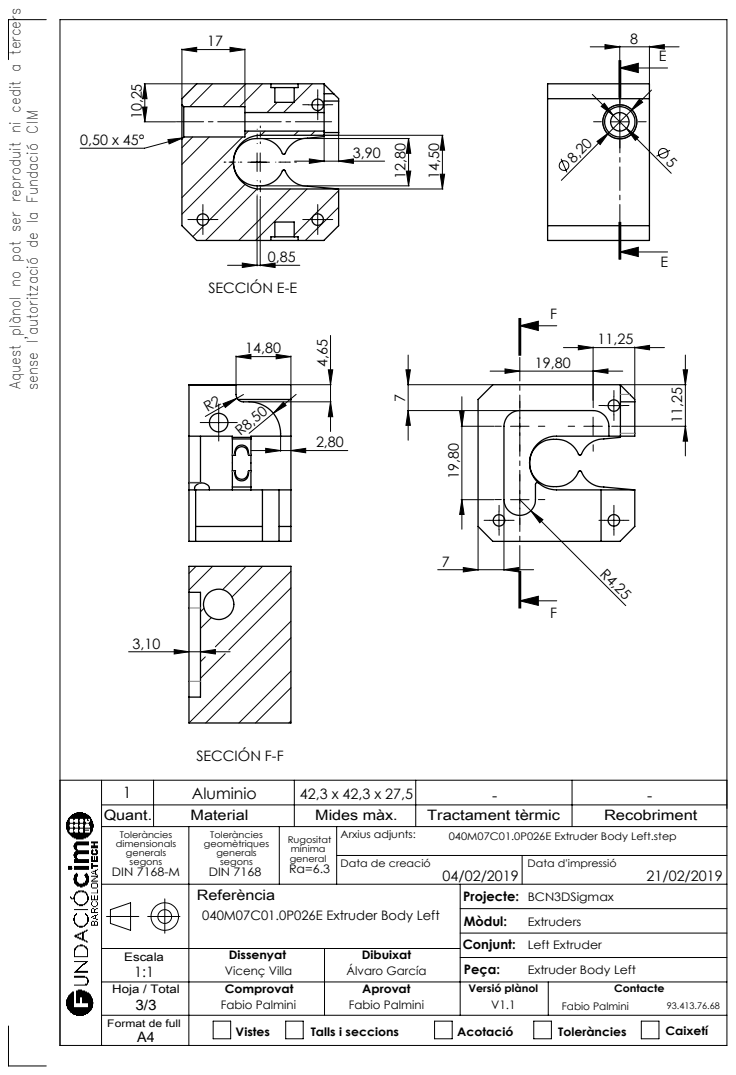
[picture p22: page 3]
Mides màx.; Tractament tèrmic; Recobriment; Data de creació; Data d'impressió; SECCIÓN E-E; SECCIÓN F-F

Aquest plànol no pot ser reproduit ni cedit a tercers

sense l'autorització de la Fundació CIM

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

Referència 040M07C01.0P026E Extruder Body Left | Projecte: BCN3DSigmax Mòdul: Extruders Conjunt: Left Extruder

Escala 1:1 | Dissenyat Vicenç Villa | Dibuixat Álvaro García

Extruder Body Left

Hoja / Total | Comprovat | Aprovat | Versió plànol | Contacte

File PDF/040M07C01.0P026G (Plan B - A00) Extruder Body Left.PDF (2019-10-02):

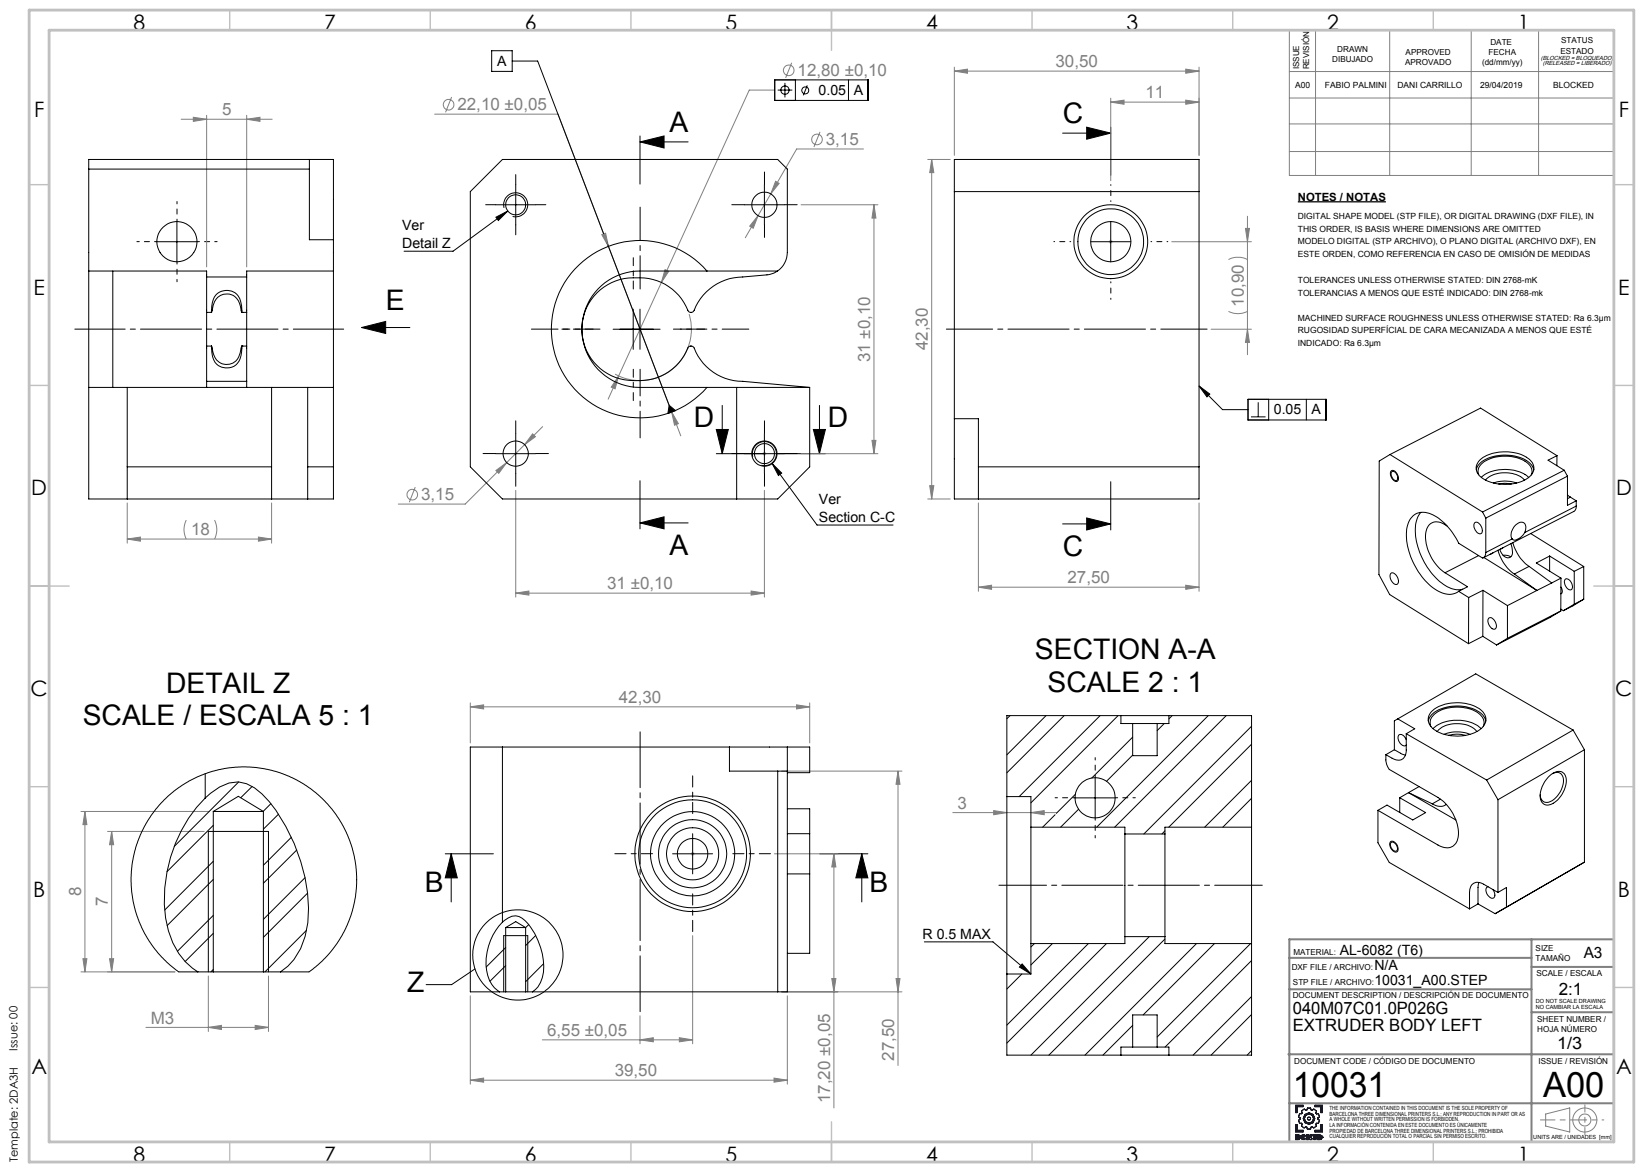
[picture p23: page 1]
SCALE / ESCALA; FABIO PALMINI; DANI CARRILLO; BLOCKED; Detail Z; Section C-C; DETAIL Z SCALE / ESCALA 5 : 1; SECTION A-A SCALE 2 : 1; R 0.5 MAX; Template: 2DA3H Issue: 00

DATE
FECHA

STATUS
ESTADO (BLOCKED = BLOQUEADO)
(RELEASED = LIBERADO)

NOTES / NOTAS
DIGITAL SHAPE MODEL (STP FILE), OR DIGITAL DRAWING (DXF FILE), IN
THIS ORDER, IS BASIS WHERE DIMENSIONS ARE OMITTED
MODELO DIGITAL (STP ARCHIVO), O PLANO DIGITAL (ARCHIVO DXF), EN
ESTE ORDEN, COMO REFERENCIA EN CASO DE OMISIÓN DE MEDIDAS

TOLERANCES UNLESS OTHERWISE STATED: DIN 2768-mK
TOLERANCIAS A MENOS QUE ESTÉ INDICADO: DIN 2768-mk

MACHINED SURFACE ROUGHNESS UNLESS OTHERWISE STATED: Ra 6.3µm
RUGOSIDAD SUPERFÍCIAL DE CARA MECANIZADA A MENOS QUE ESTÉ
INDICADO: Ra 6.3µm

MATERIAL:
DXF FILE / ARCHIVO:
STP FILE / ARCHIVO:
DOCUMENT DESCRIPTION / DESCRIPCIÓN DE DOCUMENTO
EXTRUDER BODY LEFT

DO NOT SCALE DRAWING
NO CAMBIAR LA ESCALA
SHEET NUMBER /
HOJA NÚMERO

DOCUMENT CODE / CÓDIGO DE DOCUMENTO | ISSUE / REVISIÓN A00

THE INFORMATION CONTAINED IN THIS DOCUMENT IS THE SOLE PROPERTY OF BARCELONA THREE DIMENSIONAL PRINTERS S.L.; ANY REPRODUCTION IN PART OR AS A WHOLE WITHOUT WRITTEN PERMISSION IS FORBIDDEN. LA INFORMACIÓN CONTENIDA EN ESTE DOCUMENTO ES ÚNICAMENTE PROPIEDAD DE BARCELONA THREE DIMENSIONAL PRINTERS S.L.; PROHIBIDA CUALQUIER REPRODUCIÓN TOTAL O PARCIAL SIN PERMISO ESCRITO. | UNITS ARE / UNIDADES [mm]

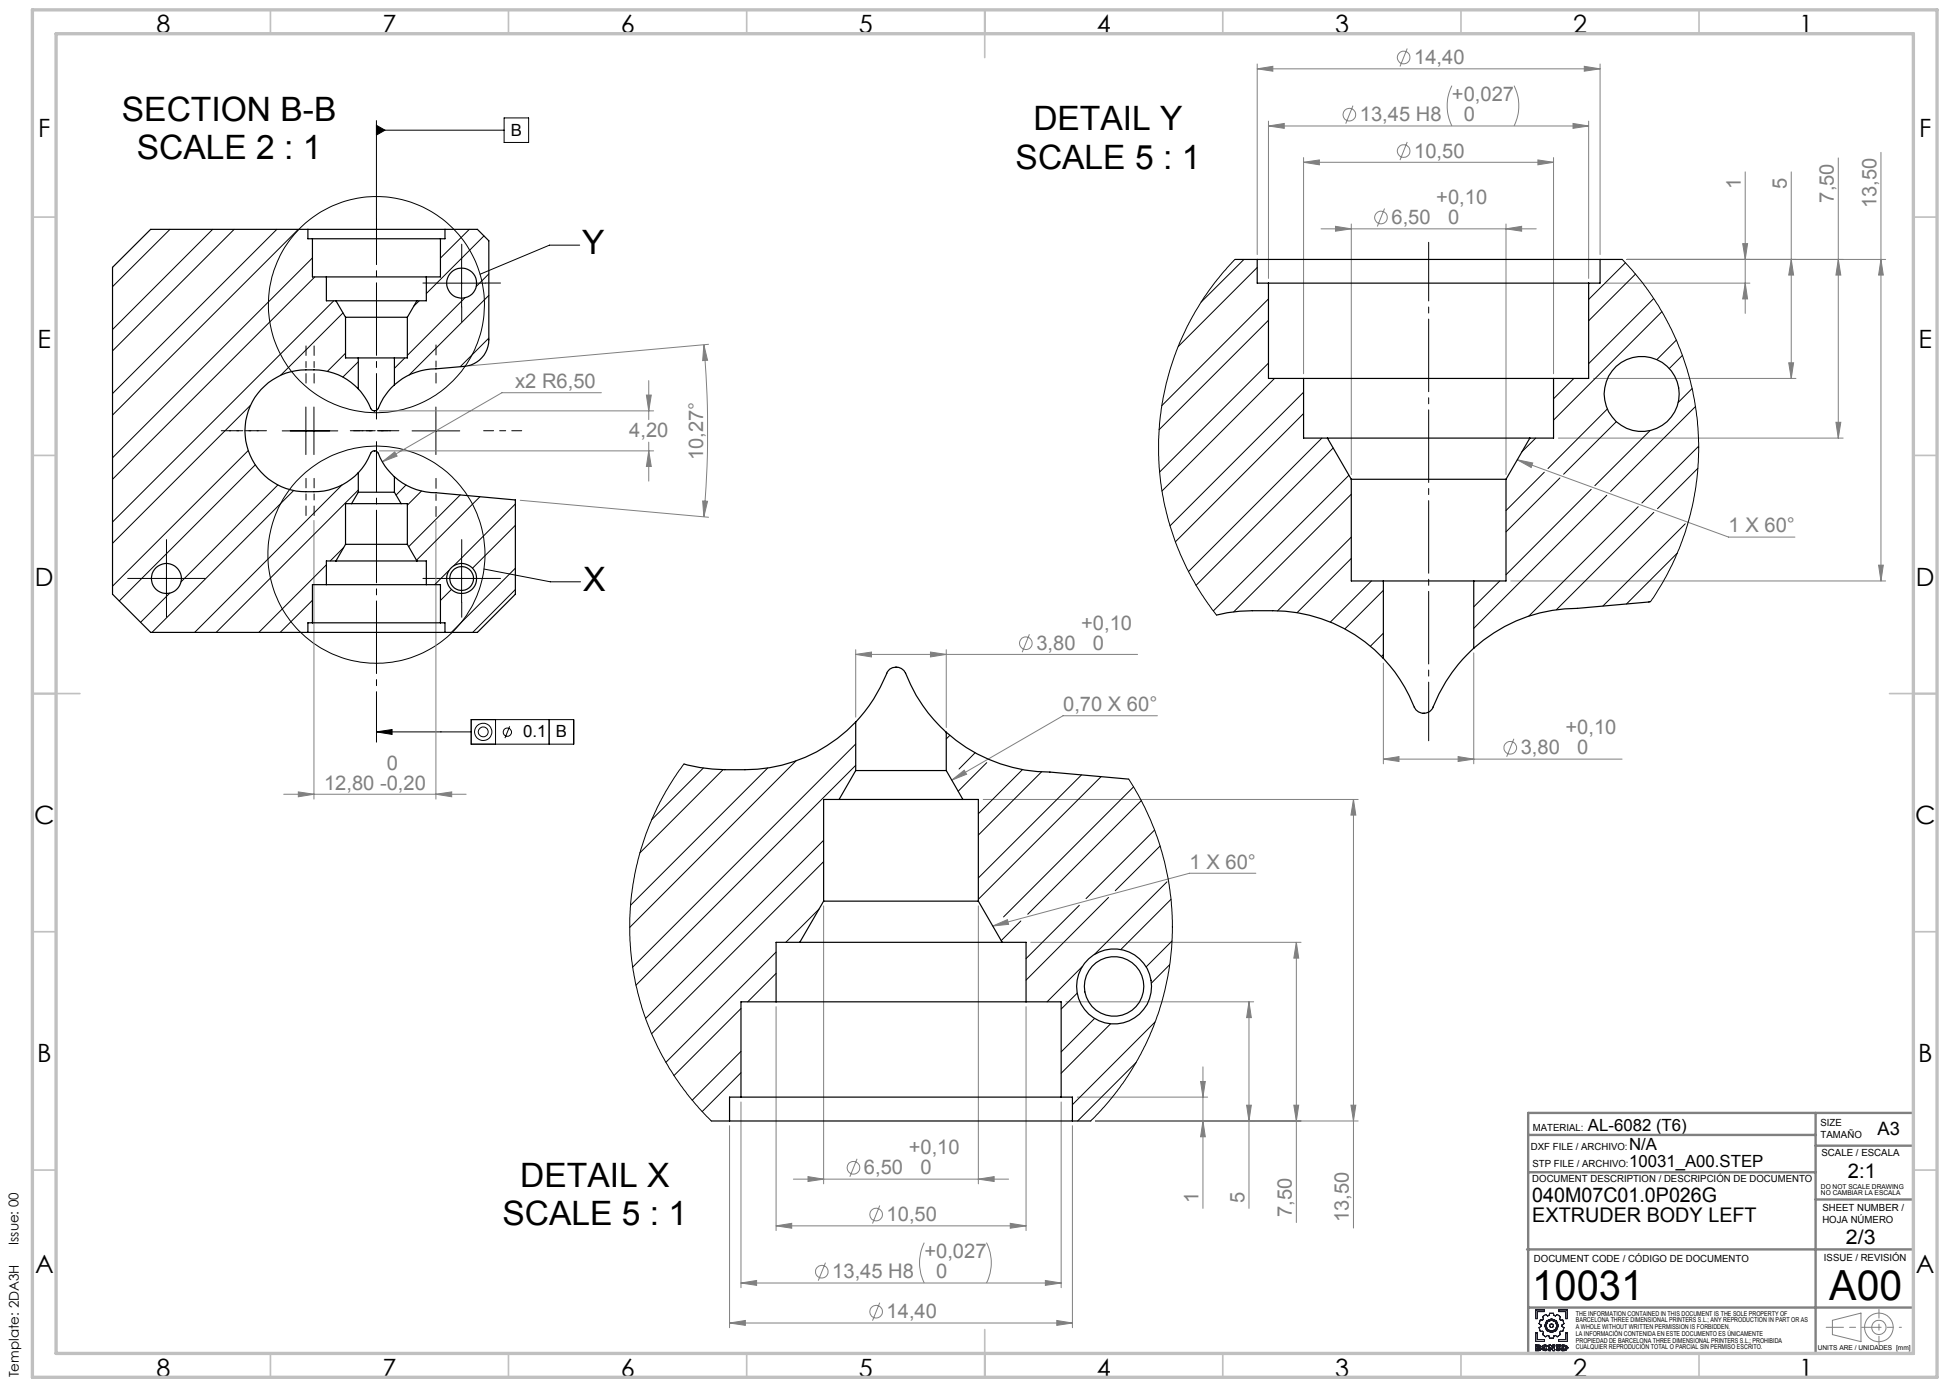
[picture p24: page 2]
DOCUMENT CODE / CÓDIGO DE DOCUMENTO; ISSUE / REVISIÓN; SCALE / ESCALA; SECTION B-B SCALE 2 : 1; DETAIL Y SCALE 5 : 1; DETAIL X SCALE 5 : 1; Template: 2DA3H Issue: 00

MATERIAL:
DXF FILE / ARCHIVO:
STP FILE / ARCHIVO:
DOCUMENT DESCRIPTION / DESCRIPCIÓN DE DOCUMENTO
EXTRUDER BODY LEFT

DO NOT SCALE DRAWING
NO CAMBIAR LA ESCALA
SHEET NUMBER /
HOJA NÚMERO

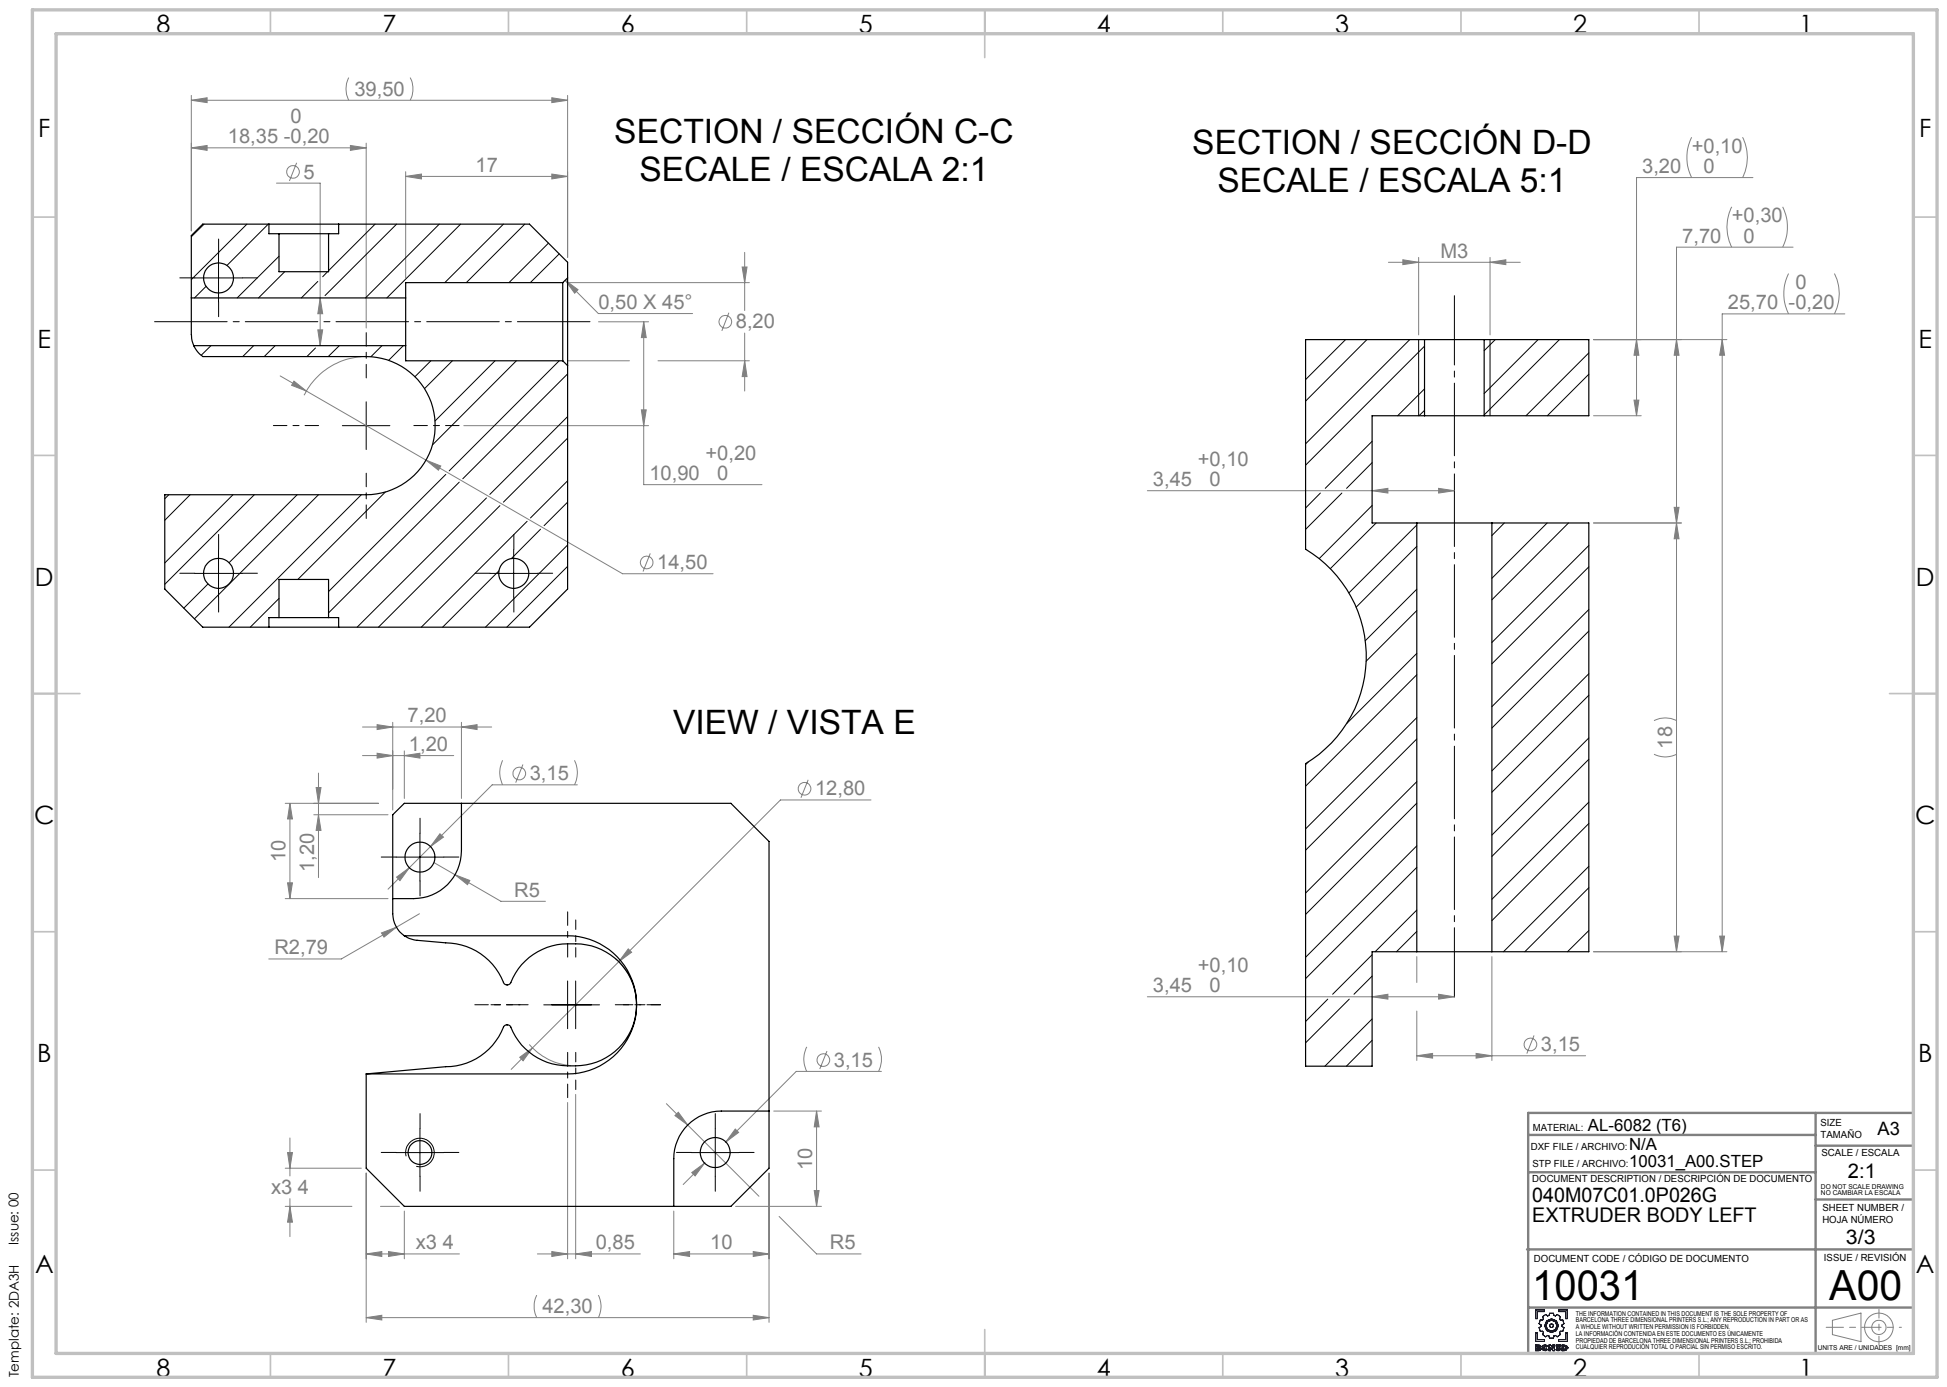
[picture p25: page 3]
DOCUMENT CODE / CÓDIGO DE DOCUMENTO; ISSUE / REVISIÓN; SCALE / ESCALA; SECTION / SECCIÓN C-C; SECALE / ESCALA 2:1; SECTION / SECCIÓN D-D SECALE / ESCALA 5:1; VIEW / VISTA E; Template: 2DA3H Issue: 00

MATERIAL:
DXF FILE / ARCHIVO:
STP FILE / ARCHIVO:
DOCUMENT DESCRIPTION / DESCRIPCIÓN DE DOCUMENTO
EXTRUDER BODY LEFT

DO NOT SCALE DRAWING
NO CAMBIAR LA ESCALA
SHEET NUMBER /
HOJA NÚMERO

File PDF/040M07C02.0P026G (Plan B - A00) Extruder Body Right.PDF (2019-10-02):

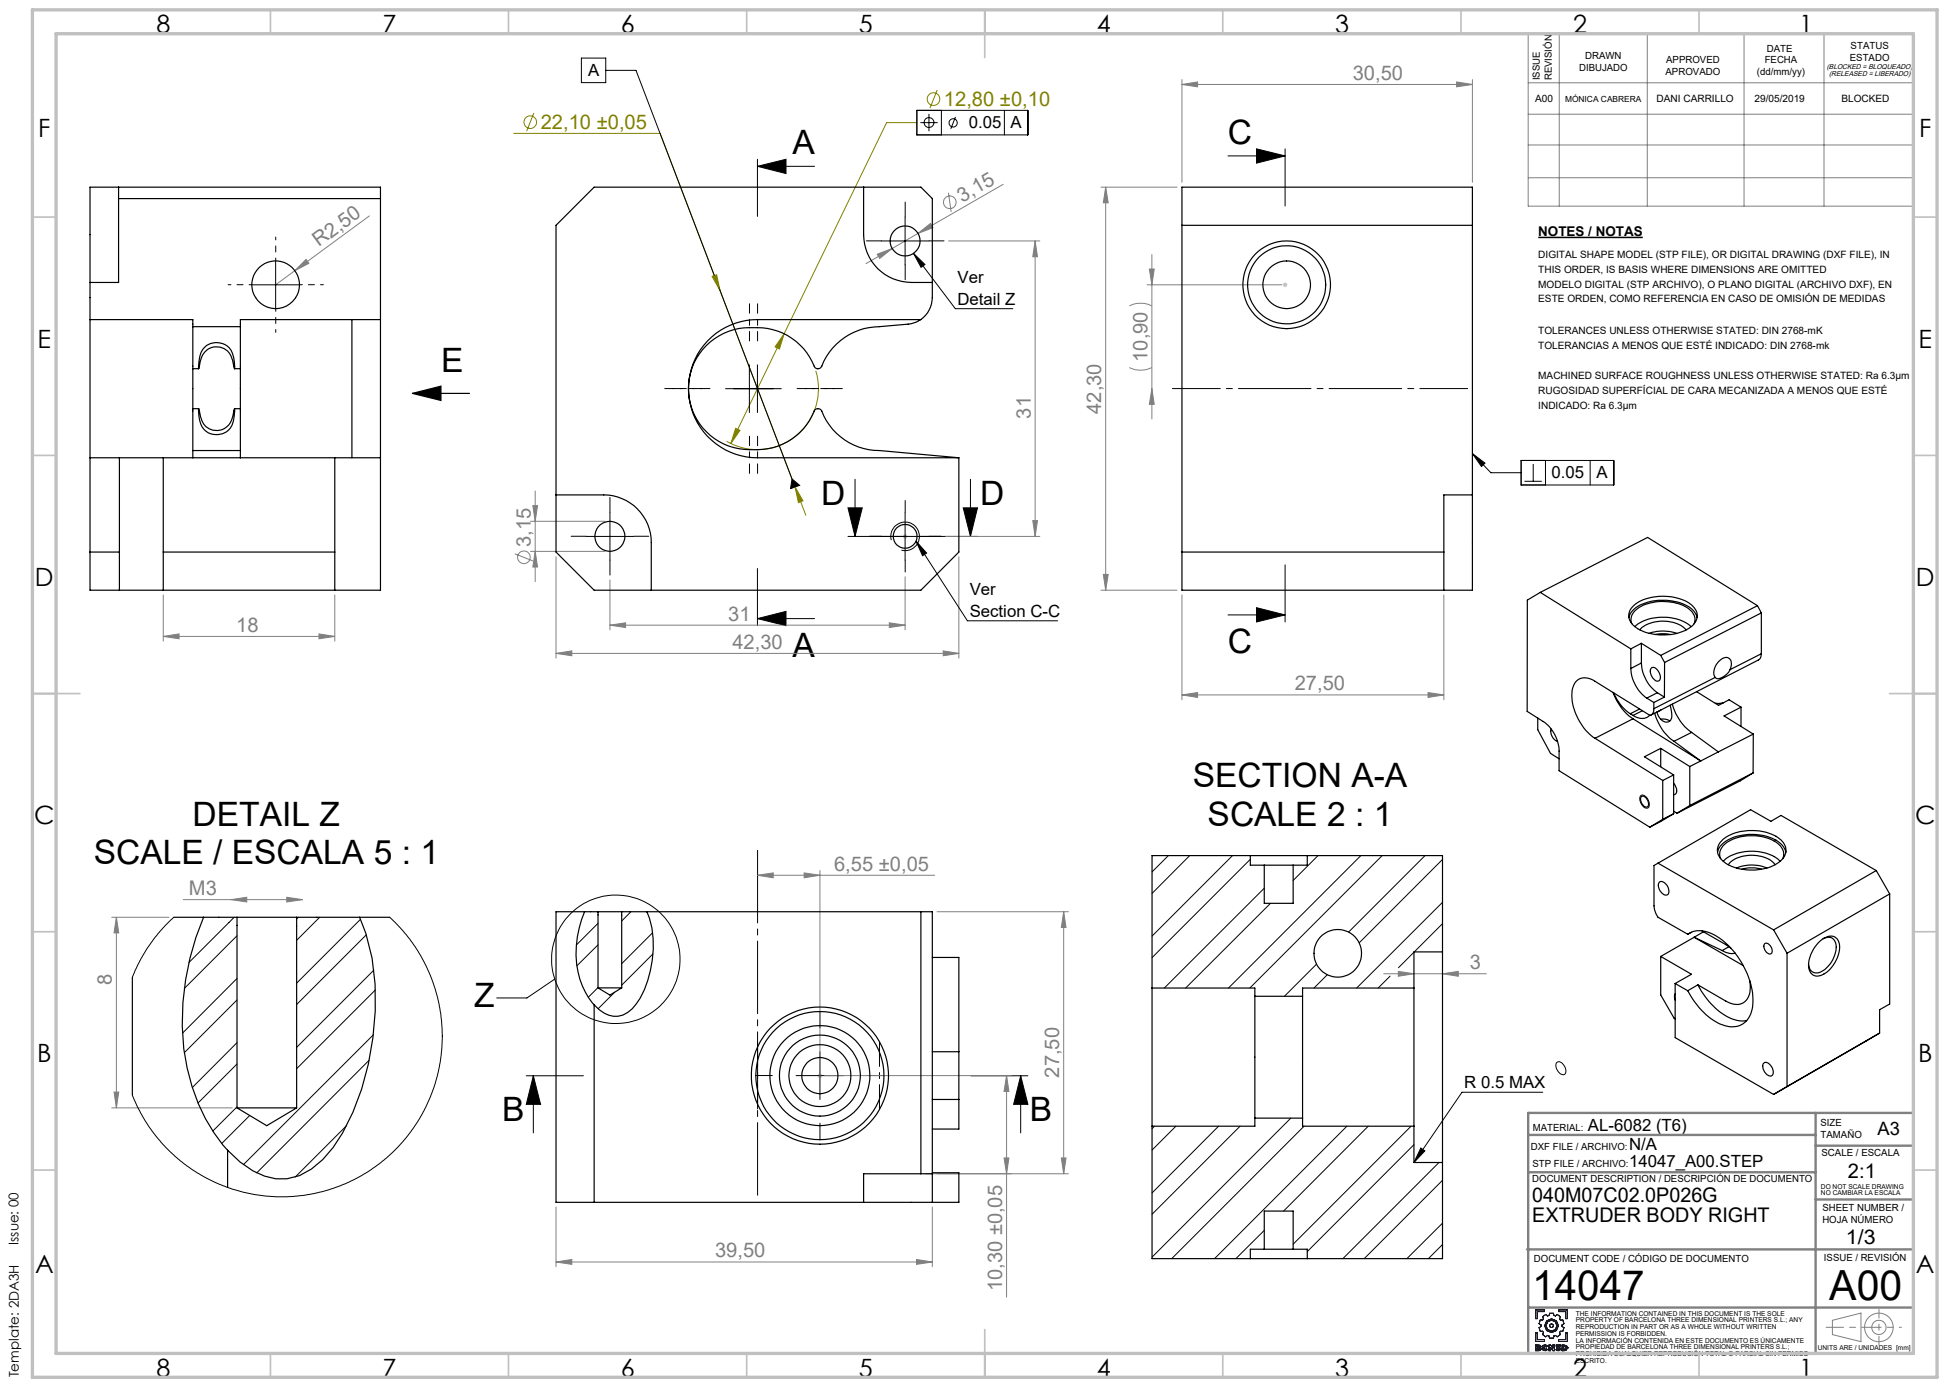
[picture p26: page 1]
SCALE / ESCALA; NOTES / NOTAS; Detail Z; Section C-C; DETAIL Z SCALE / ESCALA 5 : 1; SECTION A-A SCALE 2 : 1; R 0.5 MAX; Template: 2DA3H Issue: 00

DRAWN DIBUJADO | APPROVED APROVADO | DATE FECHA (dd/mm/yy) | STATUS ESTADO (BLOCKED = BLOQUEADO) (RELEASED = LIBERADO)

A00 | MÓNICA CABRERA | DANI CARRILLO | 29/05/2019 | BLOCKED

DIGITAL SHAPE MODEL (STP FILE), OR DIGITAL DRAWING (DXF FILE), IN
THIS ORDER, IS BASIS WHERE DIMENSIONS ARE OMITTED
MODELO DIGITAL (STP ARCHIVO), O PLANO DIGITAL (ARCHIVO DXF), EN
ESTE ORDEN, COMO REFERENCIA EN CASO DE OMISIÓN DE MEDIDAS

TOLERANCES UNLESS OTHERWISE STATED: DIN 2768-mK
TOLERANCIAS A MENOS QUE ESTÉ INDICADO: DIN 2768-mk

MACHINED SURFACE ROUGHNESS UNLESS OTHERWISE STATED: Ra 6.3µm
RUGOSIDAD SUPERFÍCIAL DE CARA MECANIZADA A MENOS QUE ESTÉ
INDICADO: Ra 6.3µm

MATERIAL:
DXF FILE / ARCHIVO:
STP FILE / ARCHIVO:
DOCUMENT DESCRIPTION / DESCRIPCIÓN DE DOCUMENTO
EXTRUDER BODY RIGHT

DO NOT SCALE DRAWING
NO CAMBIAR LA ESCALA
SHEET NUMBER /
HOJA NÚMERO

DOCUMENT CODE / CÓDIGO DE DOCUMENTO | ISSUE / REVISIÓN A00

THE INFORMATION CONTAINED IN THIS DOCUMENT IS THE SOLE PROPERTY OF BARCELONA THREE DIMENSIONAL PRINTERS S.L.; ANY REPRODUCTION IN PART OR AS A WHOLE WITHOUT WRITTEN PERMISSION IS FORBIDDEN. LA INFORMACIÓN CONTENIDA EN ESTE DOCUMENTO ES ÚNICAMENTE PROPIEDAD DE BARCELONA THREE DIMENSIONAL PRINTERS S.L.; | UNITS ARE / UNIDADES [mm]

PROHIBIDA CUALQUIER REPRODUCIÓN TOTAL O PARCIAL SIN PERMISO

ESCRITO.

DOCUMENT CODE / CÓDIGO DE DOCUMENTO; ISSUE / REVISIÓN; SCALE / ESCALA; SECTION B-B SCALE 2 : 1; DETAIL Y SCALE 5 : 1; DETAIL X SCALE 5 : 1; Template: 2DA3H Issue: 00

MATERIAL:
DXF FILE / ARCHIVO:
STP FILE / ARCHIVO:
DOCUMENT DESCRIPTION / DESCRIPCIÓN DE DOCUMENTO
EXTRUDER BODY RIGHT

DO NOT SCALE DRAWING
NO CAMBIAR LA ESCALA
SHEET NUMBER /
HOJA NÚMERO

DOCUMENT CODE / CÓDIGO DE DOCUMENTO; ISSUE / REVISIÓN; SCALE / ESCALA; SECTION / SECCIÓN C-C SECALE / ESCALA 2:1; SECTION / SECCIÓN D-D SECALE / ESCALA 5:1; VIEW / VISTA E; Template: 2DA3H Issue: 00

MATERIAL:
DXF FILE / ARCHIVO:
STP FILE / ARCHIVO:
DOCUMENT DESCRIPTION / DESCRIPCIÓN DE DOCUMENTO
EXTRUDER BODY RIGHT

DO NOT SCALE DRAWING
NO CAMBIAR LA ESCALA
SHEET NUMBER /
HOJA NÚMERO

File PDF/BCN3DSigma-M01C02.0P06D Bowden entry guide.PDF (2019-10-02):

Mides màx.; Tractament tèrmic; Recobriment; Data de creació; Data d'impressió; Vistes; Talls i seccions; Acotació; Toleràncies; Caixetí; PLA negre

Aquest plànol no pot ser reproduit ni cedit a tercers

sense l'autorització de la Fundació CIM

INFILL | LAYER HEIGHT | SHELL THICKNESS | BOTTOM/TOP THICKNESS
100% | 0.15 mm | 2 | 3

Toleràncies dimensionals generals segons DIN 7168-M | Toleràncies geomètriques generals segons DIN 7168 | Rugositat mínima general Ra=6.3 | Arxius adjunts: BCN3DSigma-M01C02.0P06D Bowden entry guide.stl

Referència BCN3DSigma-M01C02.0P06D | Projecte: BCN3DSigma Mòdul: Structure Conjunt: Structure covers

Escala 2:1 | Dissenyat Bernat Poll | Dibuixat Eric Pallarés

Bowden entry guide

Hoja / Total 1/1 | Comprovat Bernat Poll | Aprovat Bernat Poll | Versió plànol V1.0 | Contacte Bernat Poll 93.401.71.71

Format de full A4

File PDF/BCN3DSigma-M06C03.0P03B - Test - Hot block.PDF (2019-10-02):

Mides màx.; Tractament tèrmic; Recobriment; Data de creació; Data d'impressió; Vistes; Talls i seccions; Acotació; Toleràncies; Caixetí; Hot block; SECCIÓN A-A; SECCIÓN B-B; SECCIÓN C-C

Aquest plànol no pot ser reproduit ni cedit a tercers

sense l'autorització de la Fundació CIM

Toleràncies dimensionals generals segons DIN 7168-M | Toleràncies geomètriques generals segons DIN 7168 | Rugositat mínima general Ra=6.3 | Arxius adjunts: BCN3DSigma-M06C03.0P03B - Test - Hot Block.x_t

Referència BCN3DSigma-M06C03.0P03B - Test - | Projecte: BCN3DSigma Mòdul: Hotends Conjunt: Hotend

Escala 2:1 | Dissenyat Vicenç Villa | Dibuixat Vicenç Villa

Hoja / Total 1/1 | Comprovat Bernat Poll | Aprovat Bernat Poll | Versió plànol V1.1 | Contacte Vicenç Villa 93.348.70.25

Format de full A4

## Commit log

2019-10-02 added readme on CAD folder
2019-10-07 change folder name
    [(ALVARO) Conjunto Vidrio e imanes Sigma.SLDASM, 022012065.SLDPRT, 022053061.SLDPRT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]
2019-10-15 rev 0.1
    [(ALVARO) Conjunto Vidrio e imanes Sigma.SLDASM, 022012065.SLDPRT, 022053061.SLDPRT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]
